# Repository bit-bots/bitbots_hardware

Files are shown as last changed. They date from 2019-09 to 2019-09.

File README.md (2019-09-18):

# bitbots_hardware
CAD Parts and Drawings of the Robots and other Parts used by the Hamburg Bit-Bots

The Basler camera model (camera/Basler ace GigE C-Mount v01.ipt) belongs to Basler AG and can be found on their website https://www.baslerweb.com/de/produkte/kameras/flaechenkameras/ace/aca2040-35gc

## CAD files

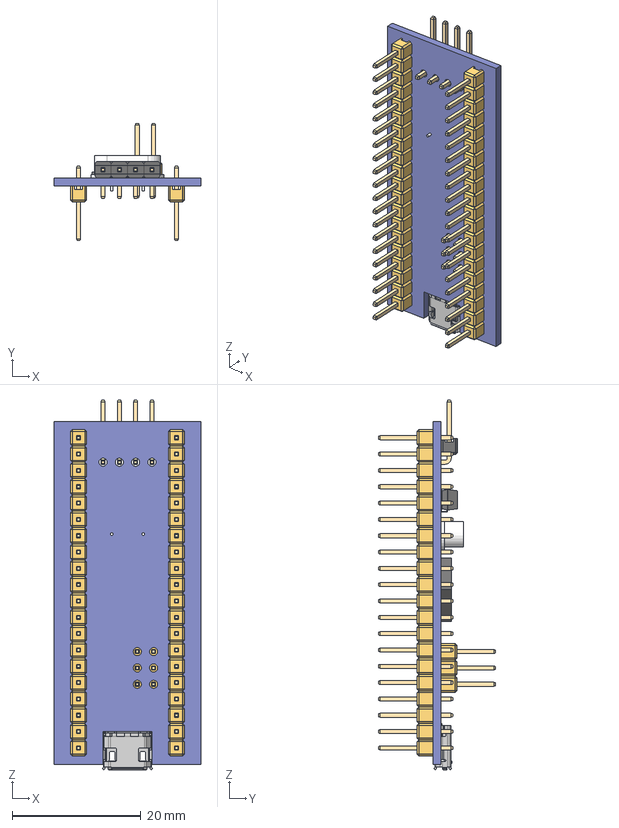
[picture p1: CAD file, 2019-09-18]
wolfgang/assembly/legs/foot/bluepill/STM32F103C8T6_Blue_Pill v6.step
22.9 x 18.3 x 57.6 mm
Oscillator_HC-49/S
STM32F103C8T6_BluePill_Board
Oscillator_MC-306
STM32_LQFP48
Tactile_SMD_5x5mm
Header_L4_10x4.8
Header_Male_2x3x11.6
Header_Male_1x20x11.6 x 2

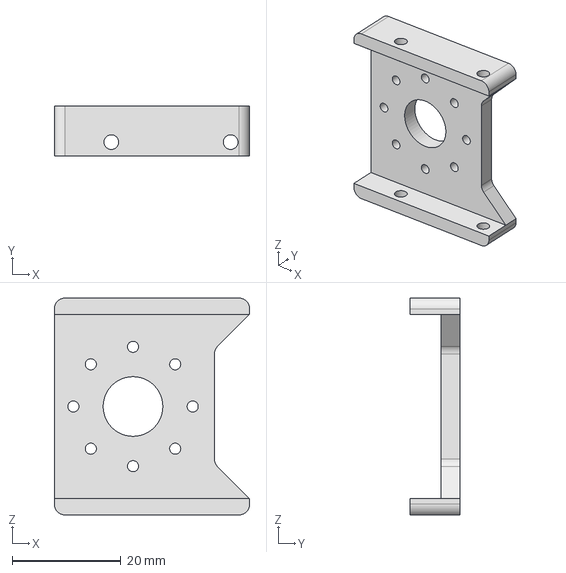
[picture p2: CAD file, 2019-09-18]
wolfgang/drawings/metal_milled/CONNECTOR_SHOULDER/connector_shoulder.stp
36.0 x 9.30 x 40.0 mm

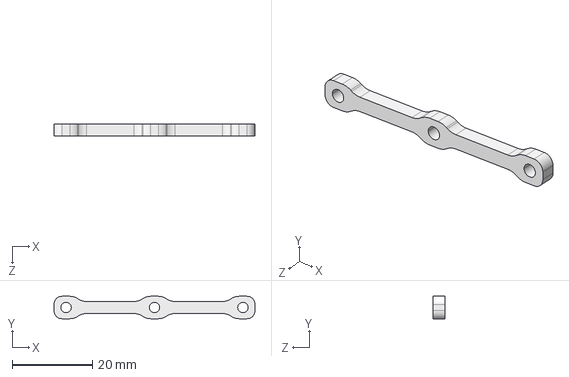
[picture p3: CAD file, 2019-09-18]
wolfgang/drawings/metal_milled/HIP_Z_SPACER/hip_z_spacer.STEP
50.0 x 5.60 x 3.00 mm

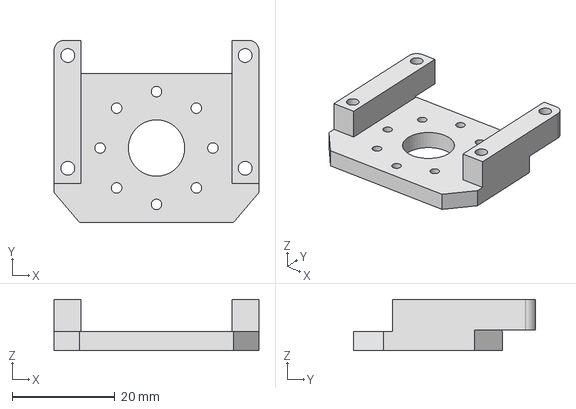
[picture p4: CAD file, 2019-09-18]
wolfgang/drawings/metal_milled/KNEE_CONNECTOR/knee_connector.stp
40.0 x 35.5 x 10.0 mm

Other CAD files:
wolfgang/drawings/carbon_parts/LOWER_ARM/lower_arm.dwg
wolfgang/drawings/carbon_parts/LOWER_LEG/lower_leg.dwg
wolfgang/drawings/carbon_parts/UPPER_ARM/upper_arm.dwg
wolfgang/drawings/carbon_parts/UPPER_LEG/upper_leg.dwg
wolfgang/drawings/metal_bent/SHOULDER/shoulder.dwg
wolfgang/drawings/metal_milled/ANKLE/ankle.dwg
wolfgang/drawings/metal_milled/TORSO_BOTTOM/torso_bottom.dwg
wolfgang/drawings/metal_milled/TORSO_TOP/torso_top.dwg
camera/Basler ace GigE C-Mount v01.ipt
camera/camera2_kurz_logitech.ipt
camera/camera2_logitech.ipt
camera/camera_and_lens.iam
camera/lens.ipt
davros/april_assembly.iam
davros/april_tag.ipt
davros/april_tag_2.ipt
davros/vision_bot_base.ipt
davros/visionbot.ipt
motor_torque_analysis/base_mx106_drive_motor.ipt
motor_torque_analysis/rotator.ipt
motor_torque_analysis/spinning_wheel.ipt
motor_torque_analysis/turntable_mx106.ipt
netzteil_case.ipt
spacer.ipt
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

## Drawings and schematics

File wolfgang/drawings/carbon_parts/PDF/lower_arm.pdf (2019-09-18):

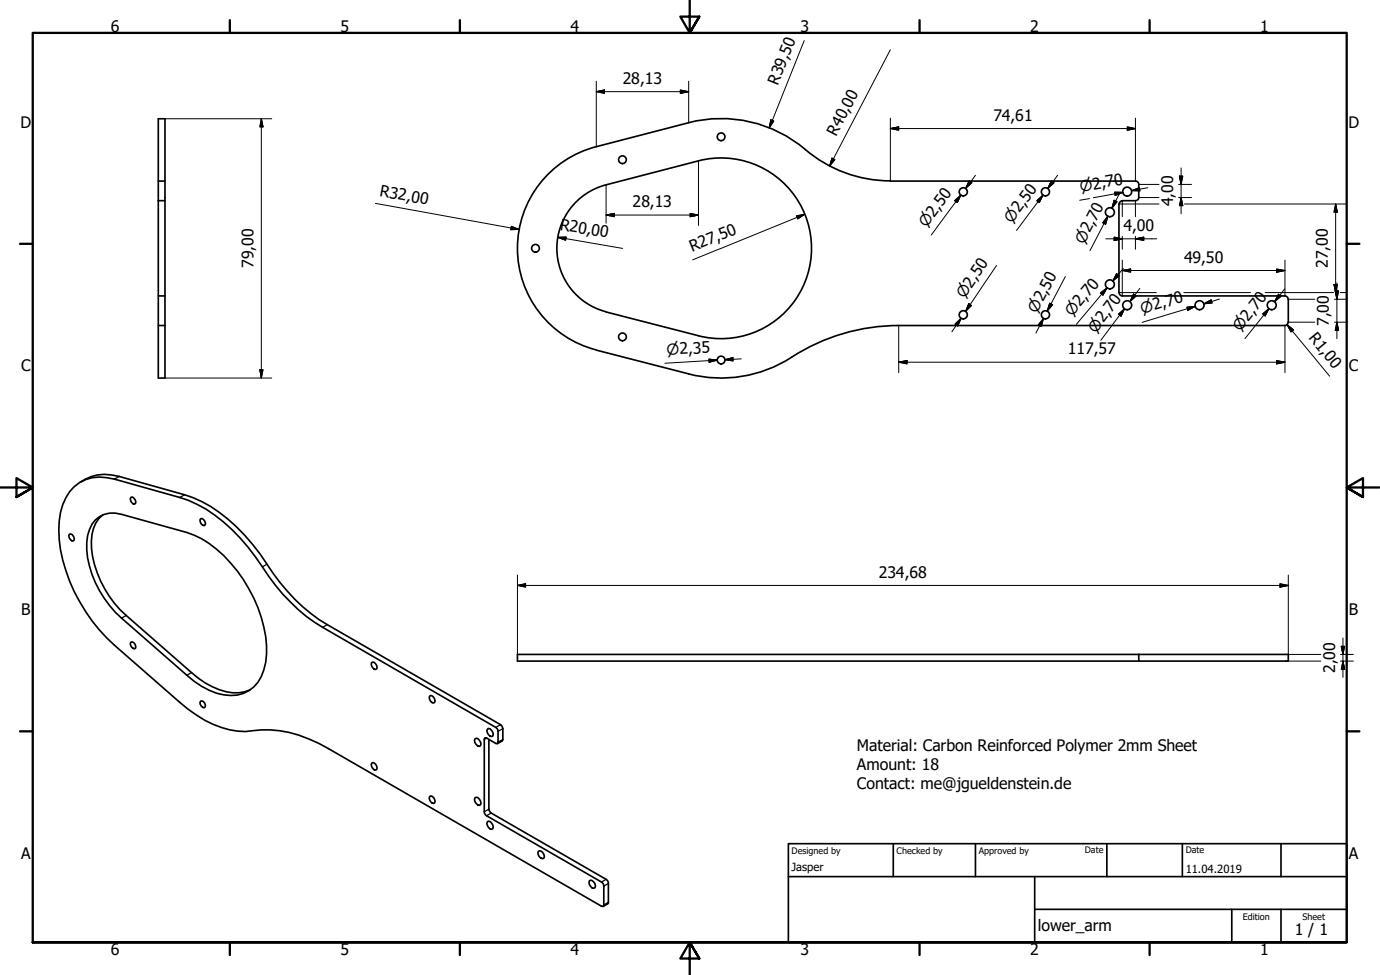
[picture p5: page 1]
Designed by; Checked by; Approved by; Date

Material: Carbon Reinforced Polymer 2mm Sheet
Amount: 18
Contact: me@jgueldenstein.de

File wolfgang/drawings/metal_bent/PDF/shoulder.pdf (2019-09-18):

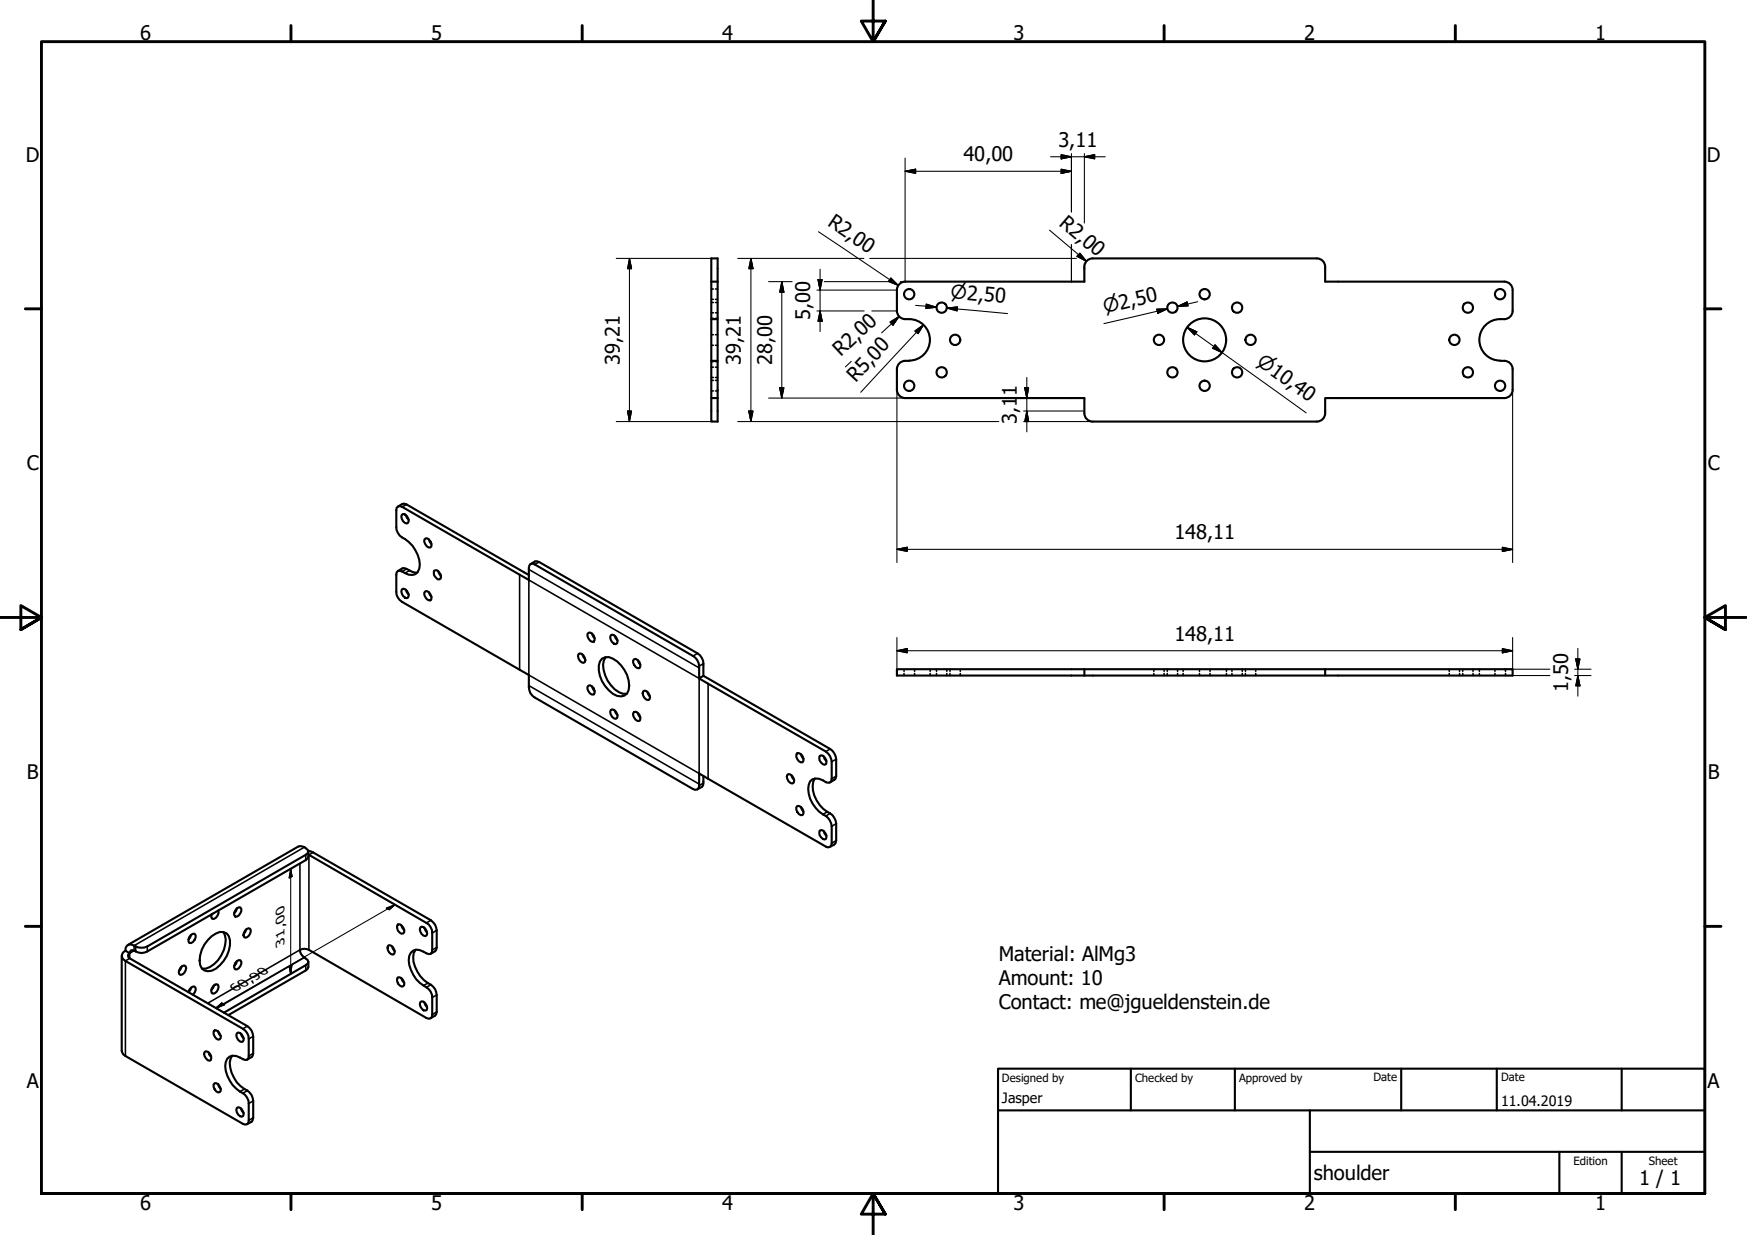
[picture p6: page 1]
Designed by; Checked by; Approved by; Date

Material: AlMg3
Amount: 10
Contact: me@jgueldenstein.de

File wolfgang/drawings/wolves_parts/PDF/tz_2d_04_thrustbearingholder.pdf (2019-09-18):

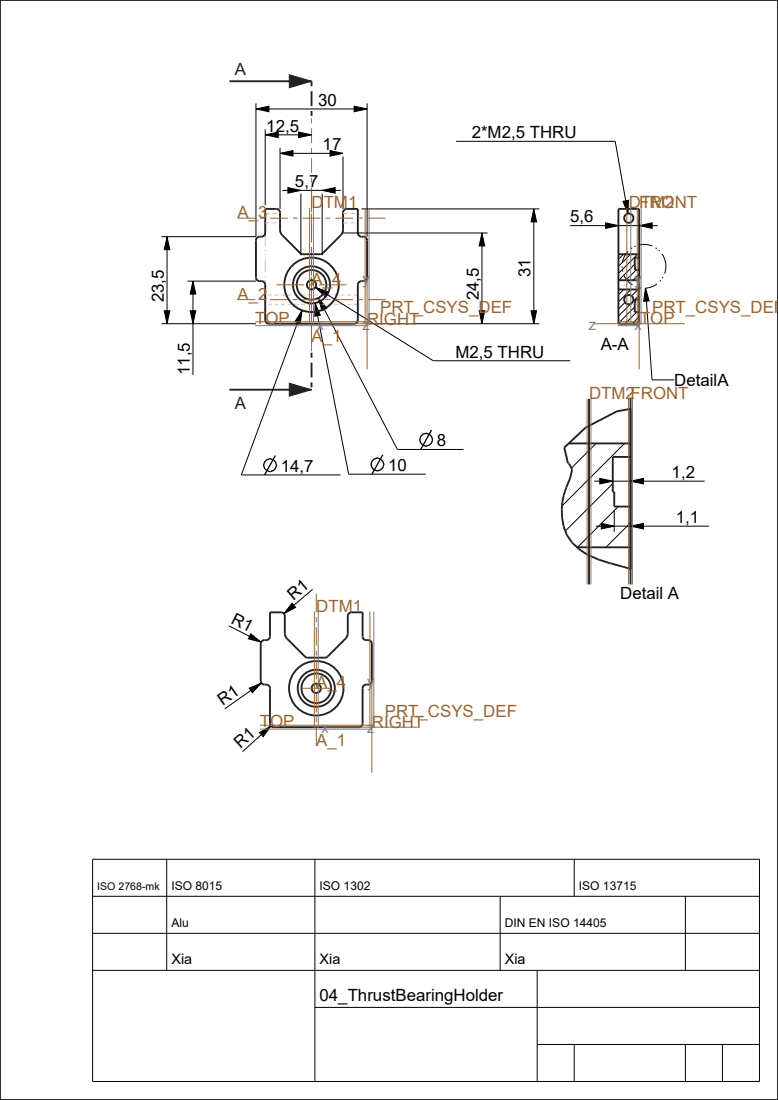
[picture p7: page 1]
2*M2,5 THRU; M2,5 THRU; DetailA; Detail A; TOP; RIGHT; DTM1; DTM2 FRONT; DTM2FRONT; PRT_CSYS_DEF

ISO 2768-mk | ISO 8015 | ISO 1302 | ISO 13715

Alu | | DIN EN ISO 14405
Xia | Xia | Xia

04_ThrustBearingHolder

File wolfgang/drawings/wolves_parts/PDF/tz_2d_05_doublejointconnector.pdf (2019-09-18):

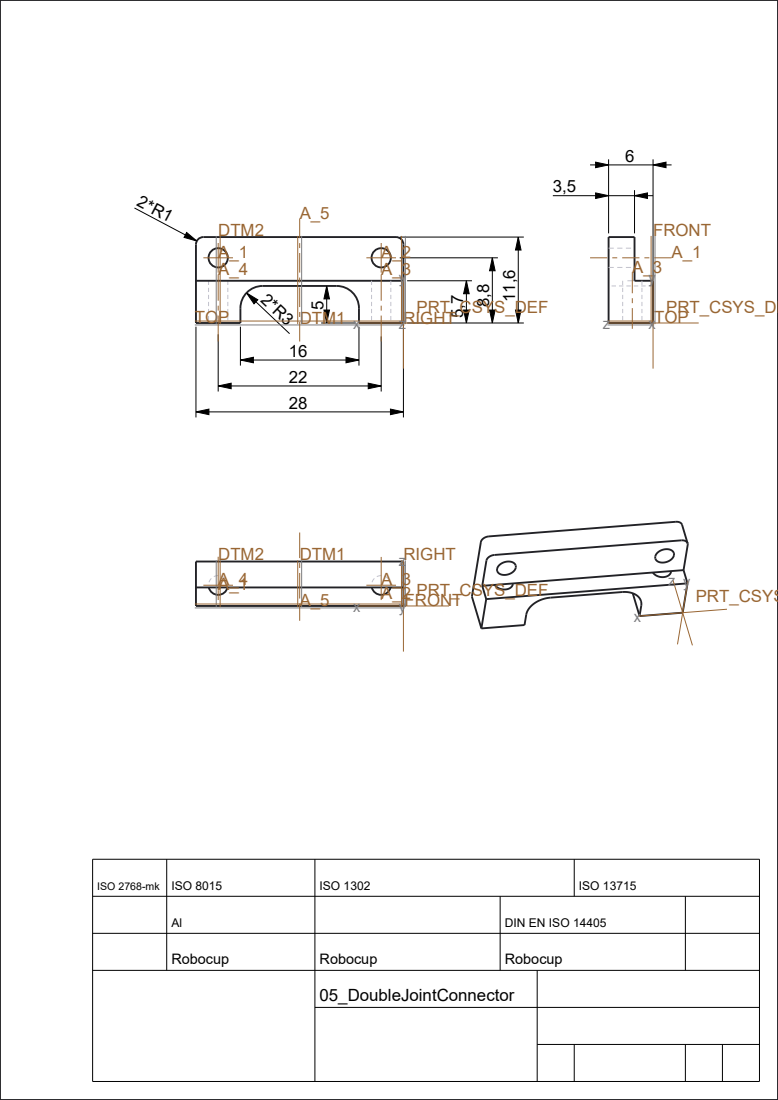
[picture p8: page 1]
TOP; DTM1; RIGHT; DTM2; FRONT; PRT_CSYS_DEF

ISO 2768-mk | ISO 8015 | ISO 1302 | ISO 13715

Al | | DIN EN ISO 14405
Robocup | Robocup | Robocup

05_DoubleJointConnector

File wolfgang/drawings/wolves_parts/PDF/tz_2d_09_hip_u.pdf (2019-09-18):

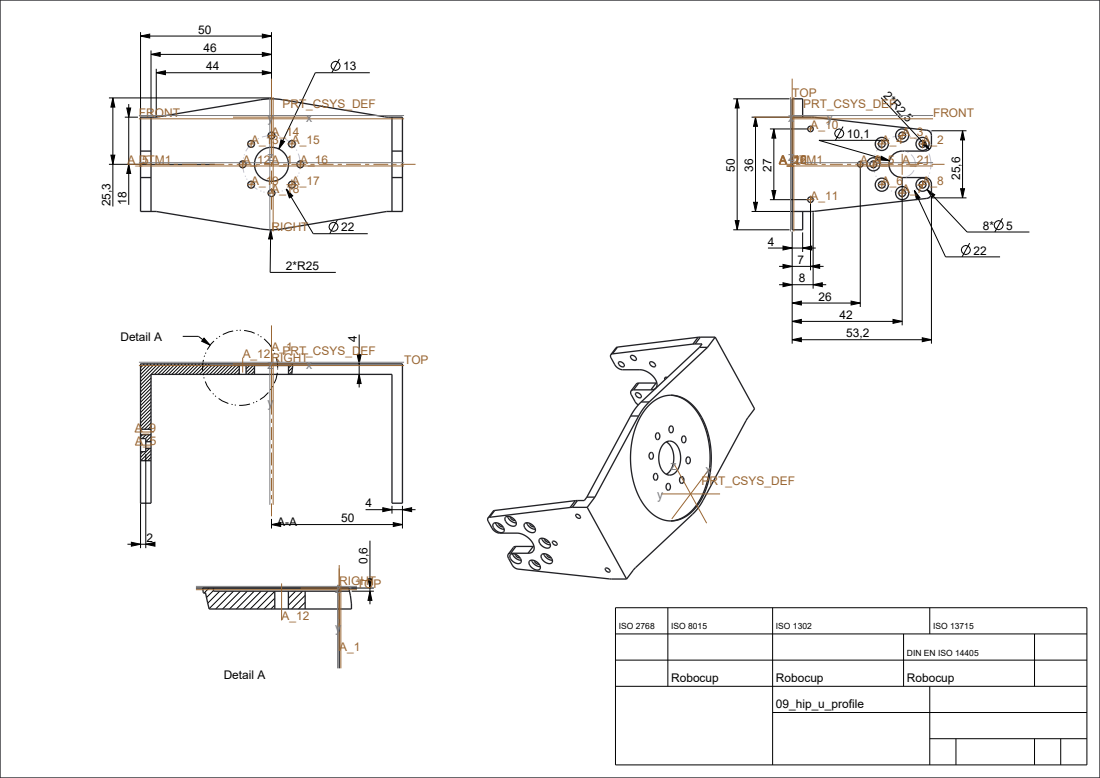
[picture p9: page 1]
Detail A; RIGHT; FRONT; DTM1; TOP; RIGHT TOP; PRT_CSYS_DEF

ISO 2768 | ISO 8015 | ISO 1302 | ISO 13715

DIN EN ISO 14405

Robocup | Robocup | Robocup

09_hip_u_profile

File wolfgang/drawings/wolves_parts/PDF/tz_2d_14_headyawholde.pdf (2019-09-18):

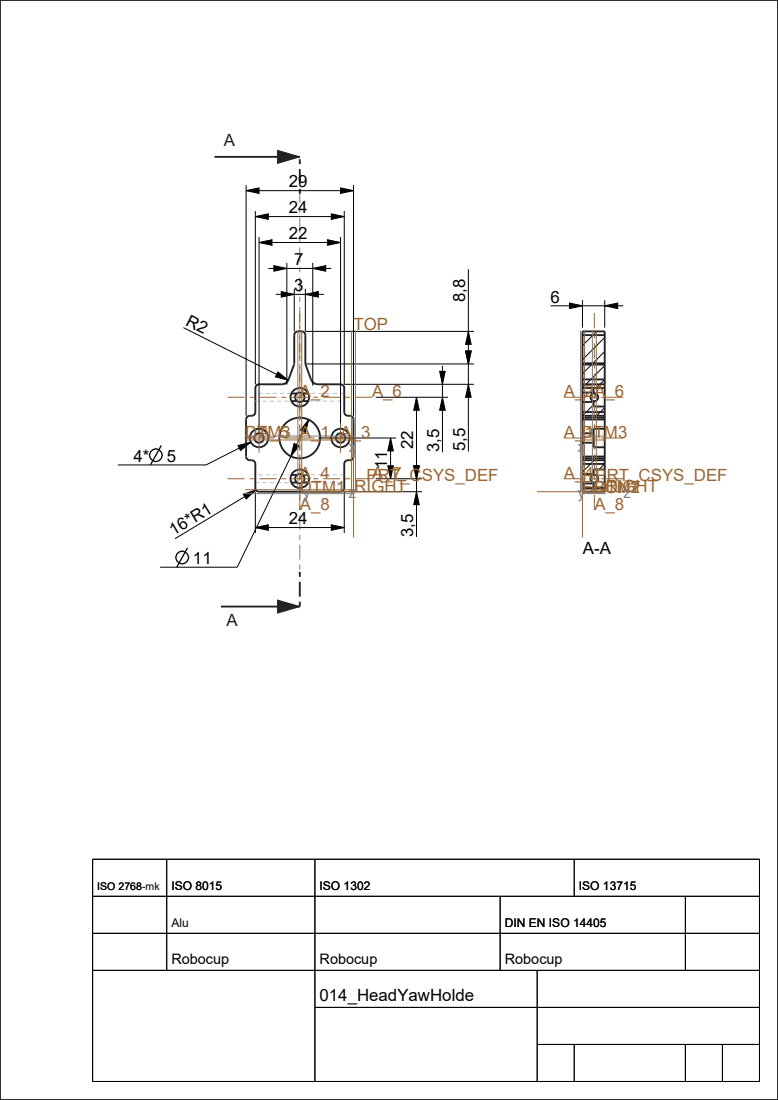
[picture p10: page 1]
RIGHT; TOP; DTM1; DTM3; FRONT DTM2 RIGHT; A_1DTM3; PRT_CSYS_DEF

24
22

ISO 2768-mk ISO 2768 | ISO 8015 | ISO 1302 | ISO 13715

Alu | | DIN EN ISO 14405
Robocup | Robocup | Robocup

014_HeadYawHolde

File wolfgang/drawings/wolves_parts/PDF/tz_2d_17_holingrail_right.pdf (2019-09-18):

25 29

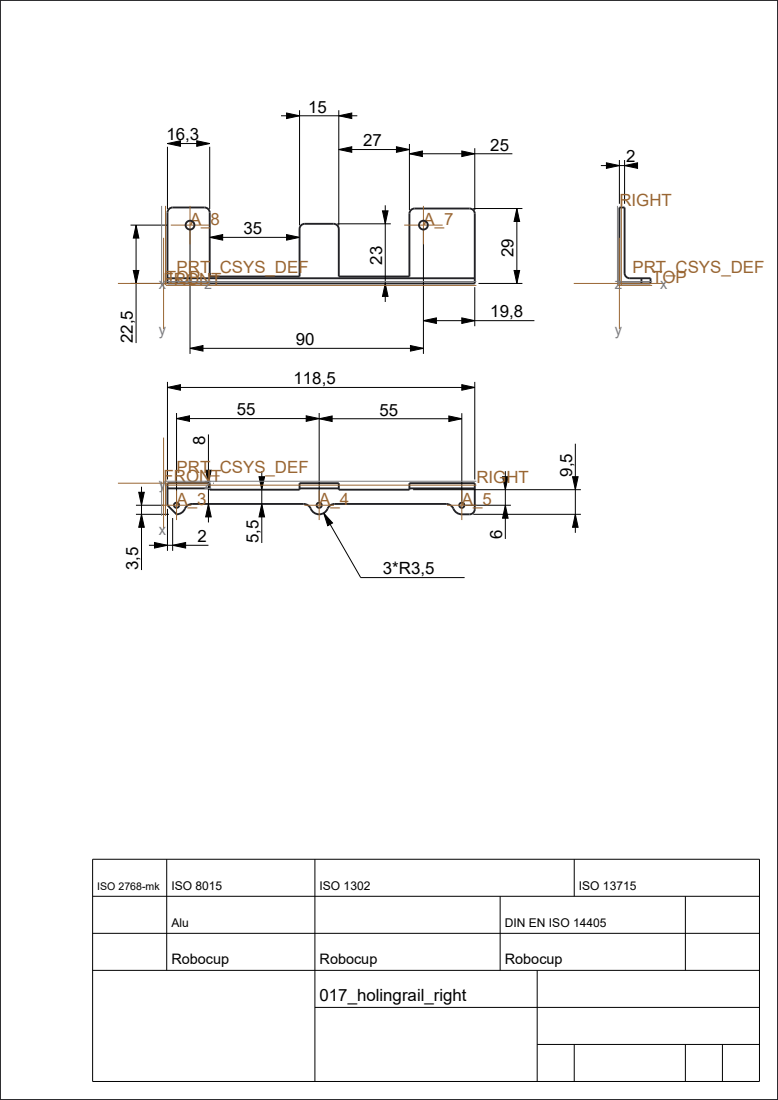
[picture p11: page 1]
FRONT TOP; RIGHT; TOP; FRONT; PRT_CSYS_DEF

ISO 2768-mk | ISO 8015 | ISO 1302 | ISO 13715

Alu | | DIN EN ISO 14405
Robocup | Robocup | Robocup

017_holingrail_right

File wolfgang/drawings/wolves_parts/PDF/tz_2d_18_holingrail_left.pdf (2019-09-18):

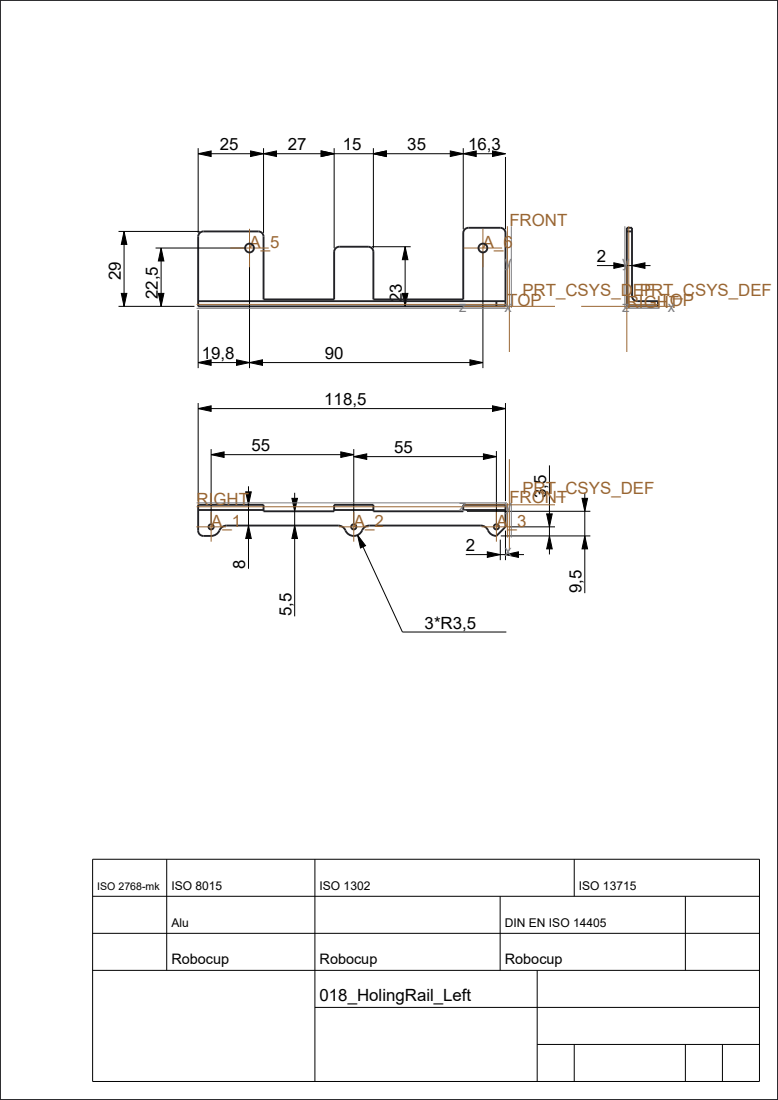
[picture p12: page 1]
TOP; FRONT; RIGHTTOP; RIGHT; PRT_CSYS_DEF

ISO 2768-mk | ISO 8015 | ISO 1302 | ISO 13715

Alu | | DIN EN ISO 14405
Robocup | Robocup | Robocup

018_HolingRail_Left

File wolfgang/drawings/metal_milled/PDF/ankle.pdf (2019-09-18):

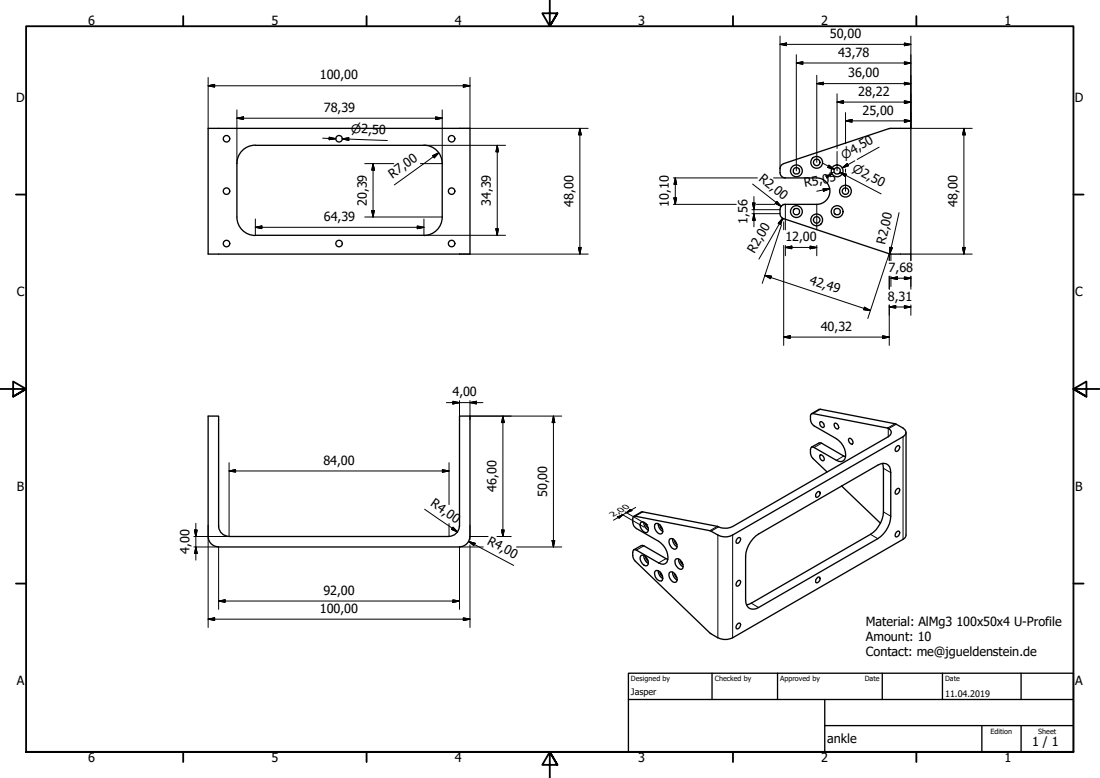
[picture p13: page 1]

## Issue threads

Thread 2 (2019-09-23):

redesign / change neck part

jgueldenstein, 2019-09-23:
the neckpart broke frequently during robocup 2019,
it needs to be more stable by using a different material or design

the issues with this part may also be resolved by #1 because the head might be shorter

jgueldenstein, 2019-09-23:
Now I am trying to print the original part in ninjaflex.
We then need to evaluate deformation and stability of the part

Closed 2020-11-18.

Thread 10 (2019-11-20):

bumpers for the inside and outside of arm to dampen impact

jgueldenstein, 2019-11-20:

jaagut, 2023-02-17:
Half-domes on top of the motor horns

jaagut, 2023-08-09:
Get inspired by new designs from CIT brains or Rhoban

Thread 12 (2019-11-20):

Knee protection to reduce cable damage

jgueldenstein, 2019-11-20:

Closed 2023-08-09.

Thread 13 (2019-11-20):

replace power cables inside motors + add transzorb

jgueldenstein, 2019-11-20:

NFiedler, 2019-12-04:
Use the situation to update the motor software

Closed 2022-07-01.

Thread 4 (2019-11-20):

New footplate

jgueldenstein, 2019-11-20:
We should have a new, more lightweight foot plate with guiding rails for the foot pressure sensors

Closed 2020-08-12.

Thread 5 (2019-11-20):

3d printed case for nuc

jgueldenstein, 2019-11-20:
We should try to print a case for the nuc to reduce the weight

It should be checked whether it is heat resistant enough.

Closed 2022-07-01.

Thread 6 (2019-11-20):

3d printed shoulder part

jgueldenstein, 2019-11-20:
diagonal like darwin,

check rules first

16stelter, 2019-12-11:
> check rules first

RoboCup 2019 rules state "The robot does not possess a configuration where it is extended longer than 1.5·Htop ." and "The minimum length of the arm, measured from the first joint, is Htop − Hleg − Hhead." as the only restrictions for arm length. A diagonal shoulder part would not conflict with these rules and even allow for longer arms if we wanted.

Another rule that references the arms is "The height of the head Hhead, including the neck, satisfies 0.05 · Htop ≤ Hhead ≤ 0.25 · Htop. Hhead is defined
as the vertical distance from the axis of the first arm joint at the shoulder to the top of the head." Since the position of the first motor in the shoulder does not change, this should not be a problem either.

Tl;dr: We're good to go.

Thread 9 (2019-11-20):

Tube around cables to prevent damage and wear

jgueldenstein, 2019-11-20:

jgueldenstein, 2019-11-21:
samples of a protection tube have been requested

SammyRamone, 2020-11-18:
our previous approach with spiral like protectors is superior

Closed 2020-11-18.

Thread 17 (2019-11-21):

better cable holder that dont damage cables

jgueldenstein, 2019-11-21:
we might use flexible material or o-rings to hold the cable

Closed 2022-07-08.

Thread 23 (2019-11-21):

replace nuts with real spacers

jgueldenstein, 2019-11-21:
This might already be solved with #4

Closed 2020-02-12.

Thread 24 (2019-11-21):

fix the battery tester to the robot

jgueldenstein, 2019-11-21:
might already be solved by #21

Closed 2022-07-01.

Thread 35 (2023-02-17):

Prevent breaking of heads

jaagut, 2023-02-17:
- [x] Testing with existing print (Made in Bangkok)
- [ ] Test other 3D printing materials/designs (e.g., Carbon fiber reinforced) → kindly ask German
- [ ] Sheet metal?
- [x] Remove head pan joint? (see #36)

jaagut, 2023-08-09:
Testing and RoboCup2023 showed, that our current heads (improved design and infill, made in Bangkok) are durable enough.

Closing as other tasks are not necessary for the moment.

Closed 2023-08-09.

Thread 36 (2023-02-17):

Test removing head pan joint

jaagut, 2023-02-17:
- [ ] Test the vision, ipm, ... when fixating the head pan joint

Flova, 2023-02-20:
I tested it on the real robot and we can look ~2 meters away, which is not that far.

Flova, 2023-02-25:
I would close this as it seems to be not feasible with the current hardware.

Closed 2023-02-25.

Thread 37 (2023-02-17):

Fix footpressure sensors

jaagut, 2023-02-17:
1. Remove white gunk and try resoldering strain gauges
2. Order new strain gauge foils (see Order project)
3. Test new ADC chip in breadboard prototype

jaagut, 2023-08-09:
New strain gauges have arrived.
Board will be replaced in favor of a new sensor-foot.

Closing as not relevant anymore...

Closed 2023-08-09.

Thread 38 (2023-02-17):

Design new hip brace part

jaagut, 2023-02-17:
for x-servos in hip pitch and roll

jaagut, 2023-08-09:
This was needed for #39, but we will not go this route in the next year, therefore closing this.

Closed 2023-08-09.

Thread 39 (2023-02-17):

Leg reinforcement

jaagut, 2023-02-17:
- [ ] Test doubling up the carbon sheets
- [ ] Replace the worst gears
    - [ ] Measure backlash of servos using 3D-printed jig (see #40)
- [ ] Use x-servos in hip pitch and roll (see #38)

jaagut, 2023-08-09:
We will go another route to improving the stability of the legs, therefore closing this.

Closed 2023-08-09.

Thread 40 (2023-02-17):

Design jig for measuring servo backlash

jaagut, 2023-02-17:

jaagut, 2023-04-18:
Done with @ayin21

Closed 2023-04-18.

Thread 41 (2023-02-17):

Prevent computer shutdown

jaagut, 2023-02-17:
This happens, when servos use a lot of power
We could use a boost converter to stabilize voltage to the PC

- [ ] Order and test boost converter (see Order project)

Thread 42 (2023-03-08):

Test actual backlash in legs

texhnolyze, 2023-03-08:
To clarify if we need software changes we want to test the actual backlash of our legs/motors:
- currently
- with serviced/new motors

timonegk, 2023-04-18:
Also evaluate recalibrating rotated by 90°

jaagut, 2023-08-09:
This has been done on Jack and Rory. Results are in our cloud storage at `BibBots-Home-Public/backlash.ods`
Motors have been swapped 90°, recalibrated and redistributed according to their performance.

Closed 2023-08-09.

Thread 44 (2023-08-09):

Reprint/Redesign torso bumpers

jaagut, 2023-08-09:
Currently, the quality of our torso bumpers is bad and they break.

We want to redo them (perhaps softer, in other materials?) and reevaluate them. Previously, evaluation has been done by letting robots fall and maximizing the time that bumpers compress.

Maybe get inspired by the designs of CIT brains or Rhoban.

jaagut, 2023-09-18:
German Had some interesting ideas of using silicone (white) or flexible resins to create absorbing parts with many links (grey) or some kind of air suspension ("bag") that gradually releases air and when standing up springs back in it's original form

The ideas were discussed by trying these demos: 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

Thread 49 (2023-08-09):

Resolve servo communication issue

jaagut, 2023-08-09:
Was ist die Ursache?
- Kabelführung
- RS485 / TTL mix verhindern

Flova, 2023-08-12:
Wobei jetzt? Wir hatten doch keine Probleme mit 1M mehr oder?

jaagut, 2023-08-15:
We have discussed or at least noted this during our meetup.

Flova, 2023-08-30:
hmm

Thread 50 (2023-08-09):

Replace PC holder

jaagut, 2023-08-09:
Our current 3d-printed PC-holder parts are breaking.
Some may be too short?

Try with different materials (TPU or Carbon-reeinforced)

Closed 2024-07-14.

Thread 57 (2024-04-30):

Metal leg spacer

texhnolyze, 2024-04-30:
Design or reuse old spacer designs for upper and lower leg.
Produce missing spacers.

Closed 2024-07-14.

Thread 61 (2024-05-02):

redesign spacers in upper leg

timonegk, 2024-05-02:

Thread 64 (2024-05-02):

check motor availability

timonegk, 2024-05-02:
Which motors are still working, which are broken, can they be repaired?

Closed 2024-07-14.

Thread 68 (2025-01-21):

Check and fix BOM

Flova, 2025-01-21:

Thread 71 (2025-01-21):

fix screw placement on lower arm l, r

confusedlama, 2025-01-21:

Closed 2025-01-21.

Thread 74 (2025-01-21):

fix screw length on left ankle motor block

confusedlama, 2025-01-21:

Closed 2025-01-21.

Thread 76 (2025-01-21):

screws on the inner hips are a bit too short

confusedlama, 2025-01-21:

confusedlama, 2025-01-21:
the screws belong to the knee subassembly which is supposed to be symmetrical but the screws on the other side probably need to have the current length which is annoying

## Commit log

2019-09-18 initial commit of cad files
    [5v_dcdc_montingplate.ipt, 64_to_106.ipt, Basler ace GigE C-Mount v01.ipt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]
2019-09-23 Adds missing ipt files for robot assembly in inventor
    [camera_holder.ipt, nuc_holdingrail_left.ipt, nuc_holdingrail_right.ipt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]
2019-09-24 camera side and nut positioning in camera mount v2.1
    [camera_lower_baseler_wolfgang_v2.1.ipt, camera_side_basler_wolfgang_v2.1.ipt]
2019-10-23 m4 stollen
    [stollen_m4.ipt, stollen_m4_spitz.ipt]
2019-10-23 reinforcements for the head
    [camera_lower_baseler_wolfgang_v2.1.ipt]
2019-10-23 head assembly and camera updated
    [camera_lower_baseler_wolfgang_v2.1.ipt, head_link.iam]
2019-10-30 lower leg spacer
    [lower_leg_spacer.ipt]
2020-02-28 added CAD files for motor torque analysis
    [base_mx106_drive_motor.ipt, rotator.ipt, spinning_wheel.ipt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]
2020-03-11 adapted CAD file
    [turntable_mx106.ipt]
